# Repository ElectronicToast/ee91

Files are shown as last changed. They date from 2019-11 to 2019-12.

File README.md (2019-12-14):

# ee91
Analog autonomous vehicle project for EE 91 at Caltech

# Contributors
- Ray Sun - Caltech BS EE '20
- Evan Yeh - Caltech BS EE '20

# Licensing
With the exception of the Caltech logo, this project is licensed according to the terms of the MIT License. The Caltech logo is (c) California Institute of Technology and used to represent this project as part of Caltech's curriculum.

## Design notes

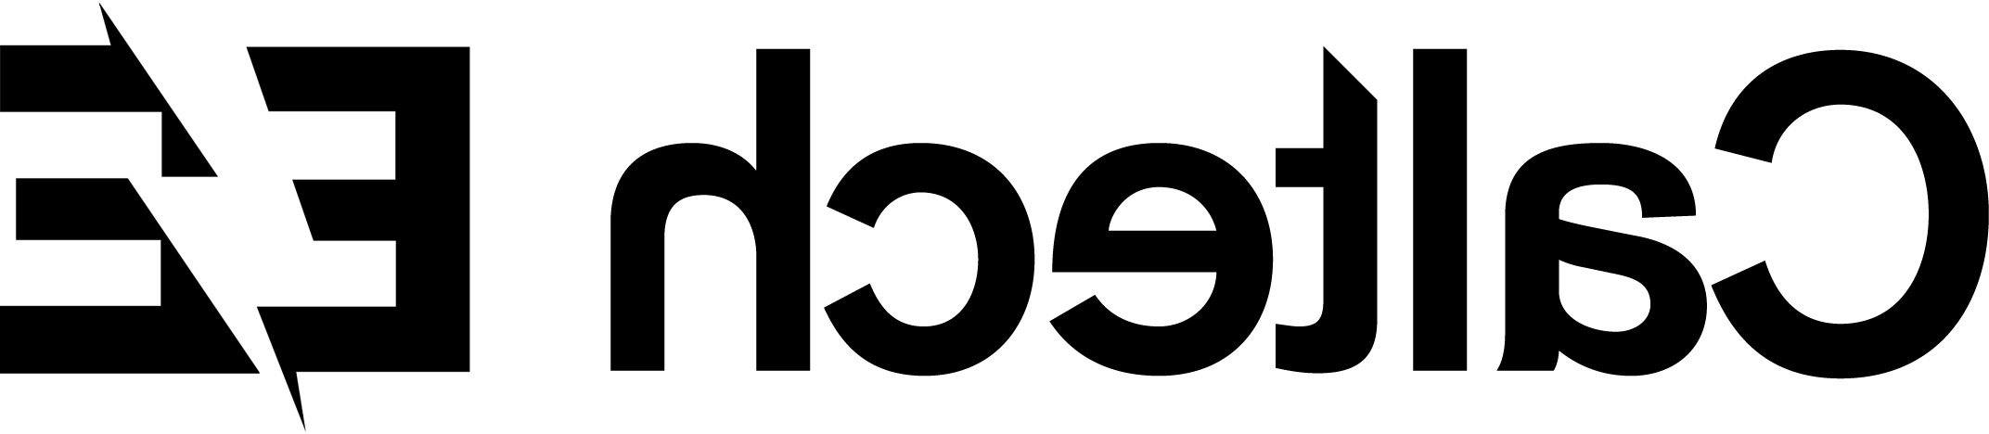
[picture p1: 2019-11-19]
Images/caltech_ee_bw_mirror.png

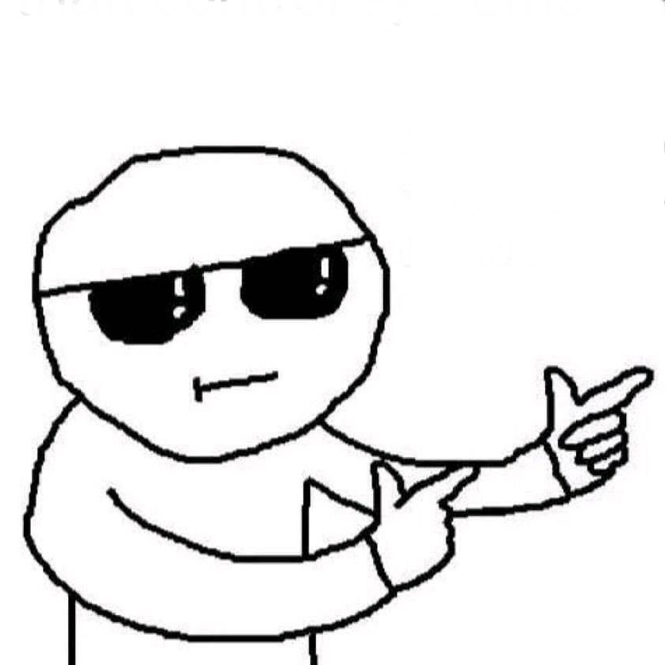
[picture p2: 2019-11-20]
Images/dude.jpg

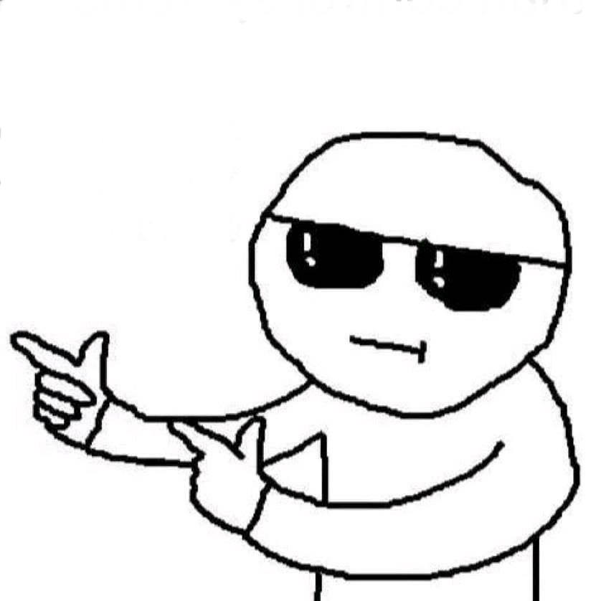
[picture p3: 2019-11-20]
Images/dude_reversed.jpg

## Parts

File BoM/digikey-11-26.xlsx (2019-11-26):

Index | Quantity | Part Number | Manufacturer Part Number | Description | Customer Reference | Available | Backorder | Unit Price | Extended Price USD
1 | 1 | 283-3029-ND | BK/GMA-200-R | FUSE GLASS 200MA 250VAC 5X20MM |  | 1 | 0 | 0.95 | 0.95
2 | 15 | 36-5005-ND | 5005 | PC TEST POINT COMPACT RED | TP_RED | 15 | 0 | 0.335 | 5.03
3 | 10 | 36-5006-ND | 5006 | PC TEST POINT COMPACT BLACK | TP_BLACK | 10 | 0 | 0.35 | 1.75
4 | 15 | 36-5007-ND | 5007 | PC TEST POINT COMPACT WHITE | TP_WHITE | 15 | 0 | 0.309 | 4.64
5 | 30 | 399-1177-1-ND | C0805C104Z5VACTU | CAP CER 0.1UF 50V Y5V 0805 | 0.1UF | 30 | 0 | 0.057 | 1.71
6 | 10 | 399-8039-1-ND | C0805C221M5RACTU | CAP CER 220PF 50V X7R 0805 | 220PF | 10 | 0 | 0.067 | 0.67
7 | 5 | 1276-2370-1-ND | CL10F334ZA8NNNC | CAP CER 0.33UF 25V Y5V 0603 | 0.33UF | 5 | 0 | 0.1 | 0.50
8 | 10 | RMCF0805FT3K90CT-ND | RMCF0805FT3K90 | RES 3.9K OHM 1% 1/8W 0805 | 3.9K | 10 | 0 | 0.027 | 0.27
9 | 10 | RMCF0805FT33K0CT-ND | RMCF0805FT33K0 | RES 33K OHM 1% 1/8W 0805 | 33K | 10 | 0 | 0.027 | 0.27
10 | 10 | RMCF0805FT39K0CT-ND | RMCF0805FT39K0 | RES 39K OHM 1% 1/8W 0805 | 39K | 10 | 0 | 0.027 | 0.27
11 | 10 | RMCF0805FT100KCT-ND | RMCF0805FT100K | RES 100K OHM 1% 1/8W 0805 | 100K | 10 | 0 | 0.027 | 0.27
12 | 5 | TC33X-102ECT-ND | TC33X-2-102E | TRIMMER 1K OHM 0.1W J LEAD TOP | 1K | 5 | 0 | 0.28 | 1.40
13 | 3 | TC33X-103ECT-ND | TC33X-2-103E | TRIMMER 10K OHM 0.1W J LEAD TOP | 10K | 3 | 0 | 0.28 | 0.84
14 | 5 | TC33X-104ECT-ND | TC33X-2-104E | TRIMMER 100K OHM 0.1W J LEAD TOP | 100K | 5 | 0 | 0.28 | 1.40
15 | 5 | 1N4148WTPMSCT-ND | 1N4148W-TP | DIODE GEN PURP 100V 150MA SOD123 |  | 5 | 0 | 0.13 | 0.65
16 | 3 | 296-1336-1-ND | TLC555CDR | IC OSC SGL TIMER 2.1MHZ 8-SOIC |  | 3 | 0 | 0.75 | 1.50
17 | 3 | 1727-6034-1-ND | 74HC1G04GV,125 | IC INVERTER 1CH 1-INP 5TSOP |  | 3 | 0 | 0.3 | 0.60
18 | 3 | 497-2345-1-ND | ULN2003D1013TR | IC PWR RELAY 7NPN 1:1 16SO |  | 3 | 0 | 0.52 | 1.04
19 | 10 | RMCF0805FT1K00CT-ND | RMCF0805FT1K00 | RES 1K OHM 1% 1/8W 0805 | 1k | 10 | 0 | 0.027 | 0.27
20 | 10 | RMCF0805FT10K0CT-ND | RMCF0805FT10K0 | RES 10K OHM 1% 1/8W 0805 | 10k | 10 | 0 | 0.027 | 0.27
21 | 15 | 399-17617-1-ND | C0805C103K1RAC7210 | CAP CER SMD 0805 .01UF 100V X7R | 0.01uF | 15 | 0 | 0.068 | 1.02
22 | 10 | 1276-6455-1-ND | CL21A106KOQNNNG | CAP CER 10UF 16V X5R 0805 | 10uF | 10 | 0 | 0.097 | 0.97
23 | 10 | RMCF0805FT4K70CT-ND | RMCF0805FT4K70 | RES 4.7K OHM 1% 1/8W 0805 | 4.7k | 10 | 0 | 0.027 | 0.27
24 | 3 | TC33X-2-504ECT-ND | TC33X-2-504E | TRIMMER 500K OHM 0.1W J LEAD TOP | 500k | 3 | 0 | 0.28 | 0.84
25 | 1 | 1568-DEV-15583-ND | DEV-15583 | TEENSY 4.0 |  | 1 | 0 | 22.5 | 22.50

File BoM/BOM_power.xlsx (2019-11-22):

RefDes | Value | Name | Manufacturer | Quantity | Buy
VCC, -VCC |  | TESTPOINT RED |  | 2 | https://www.digikey.com/products/en?mpart=5005&v=36
GND |  | TESTPOINT BLACK |  | 1 | https://www.digikey.com/product-detail/en/keystone-electronics/5006/36-5006-ND/255330
J1, J2, J3, J4 |  | JST_XH_3 |  | 4 | https://www.digikey.com/product-detail/en/jst-sales-america-inc/B3B-XH-A-LF-SN/455-2248-ND/1651046
J5, J6 |  | JST_XH_2 |  | 2 | https://www.digikey.com/product-detail/en/jst-sales-america-inc/B2B-XH-A-LF-SN/455-2247-ND/1651045

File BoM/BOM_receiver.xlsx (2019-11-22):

RefDes | Value | Name | Manufacturer | Quantity | Buy
VCC, -VCC |  | TESTPOINT RED |  | 4 | https://www.digikey.com/products/en?mpart=5005&v=36
GND |  | TESTPOINT BLACK |  | 2 | https://www.digikey.com/product-detail/en/keystone-electronics/5006/36-5006-ND/255330
BP, GAIN, US_IN |  | TESTPOINT WHITE |  | 6 | https://www.digikey.com/product-detail/en/keystone-electronics/5007/36-5007-ND/255331
C7, C8 | 0.01uF | CAP_0805 |  | 4
C3, C4, C5, C6, C9 | 0.1uF | CAP_0805 |  | 10
C1, C2 | 220pF | CAP_0805 |  | 4
C10, C11 | 10uF | CAP_0805 |  | 4
R3 | 3.9k | RES_0805 |  | 2
R1 | 4.7k | RES_0805 |  | 2
R5 | 10k | RES_0805 |  | 2
R4 | 100k | RES_0805 |  | 2
D1 |  | 1N4148 |  | 2 | https://www.digikey.com/product-detail/en/on-semiconductor/1N4148WS/1N4148WSFSCT-ND/1873821
J1, J2 |  | JST_XH_2 | JST | 4 | https://www.digikey.com/product-detail/en/jst-sales-america-inc/B2B-XH-A-LF-SN/455-2247-ND/1651045
J3 |  | JST_XH_3 | JST | 2 | https://www.digikey.com/product-detail/en/jst-sales-america-inc/B3B-XH-A-LF-SN/455-2248-ND/1651046
R2 | 500k | TC33X-2_500k | Bourns | 2 | https://www.digikey.com/product-detail/en/bourns-inc/TC33X-2-504E/TC33X-2-504ETR-ND/2566902
U1 |  | AD826AR | Analog Devices | 2 | https://www.digikey.com/product-detail/en/analog-devices-inc/AD826ARZ/AD826ARZ-ND/620949

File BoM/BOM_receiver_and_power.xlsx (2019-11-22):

Value | Name | Manufacturer | Quantity | Buy
 | TESTPOINT RED |  | 6 | https://www.digikey.com/products/en?mpart=5005&v=36
 | TESTPOINT BLACK |  | 3 | https://www.digikey.com/product-detail/en/keystone-electronics/5006/36-5006-ND/255330
 | TESTPOINT WHITE |  | 6 | https://www.digikey.com/product-detail/en/keystone-electronics/5007/36-5007-ND/255331
0.01uF | CAP_0805 |  | 4
0.1uF | CAP_0805 |  | 10
220pF | CAP_0805 |  | 4
10uF | CAP_0805 |  | 4
3.9k | RES_0805 |  | 2
4.7k | RES_0805 |  | 2
10k | RES_0805 |  | 2
100k | RES_0805 |  | 2
500k | TC33X-2_500k | Bourns | 2 | https://www.digikey.com/product-detail/en/bourns-inc/TC33X-2-504E/TC33X-2-504ETR-ND/2566902
 | 1N4148 |  | 2 | https://www.digikey.com/product-detail/en/on-semiconductor/1N4148WS/1N4148WSFSCT-ND/1873821
 | JST_XH_2 | JST | 6 | https://www.digikey.com/product-detail/en/jst-sales-america-inc/B2B-XH-A-LF-SN/455-2247-ND/1651045
 | JST_XH_3 | JST | 6 | https://www.digikey.com/product-detail/en/jst-sales-america-inc/B3B-XH-A-LF-SN/455-2248-ND/1651046
 | AD826AR | Analog Devices | 2 | https://www.digikey.com/product-detail/en/analog-devices-inc/AD826ARZ/AD826ARZ-ND/620949

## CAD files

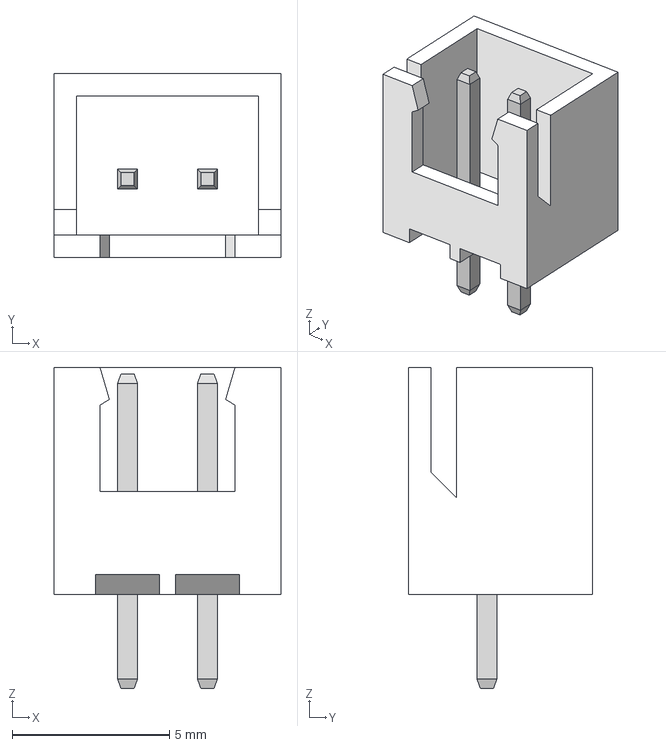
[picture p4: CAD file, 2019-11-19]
3D Models/JST - XH - Thru (V) - 2Pin - 2.54mm.stp
7.21 x 5.84 x 10.2 mm

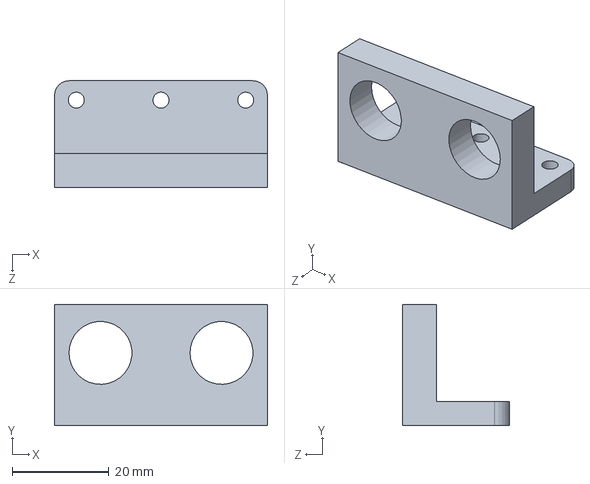
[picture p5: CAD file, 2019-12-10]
3DPrints/transducermount/transducermount.SLDPRT
44.0 x 25.0 x 22.0 mm

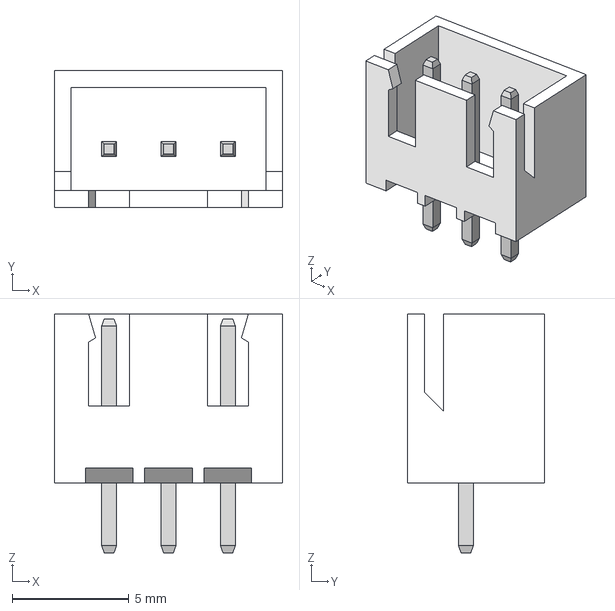
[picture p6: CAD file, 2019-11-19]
3D Models/JST - XH - Thru (V) - 3Pin - 2.54mm.stp
9.75 x 5.84 x 10.2 mm

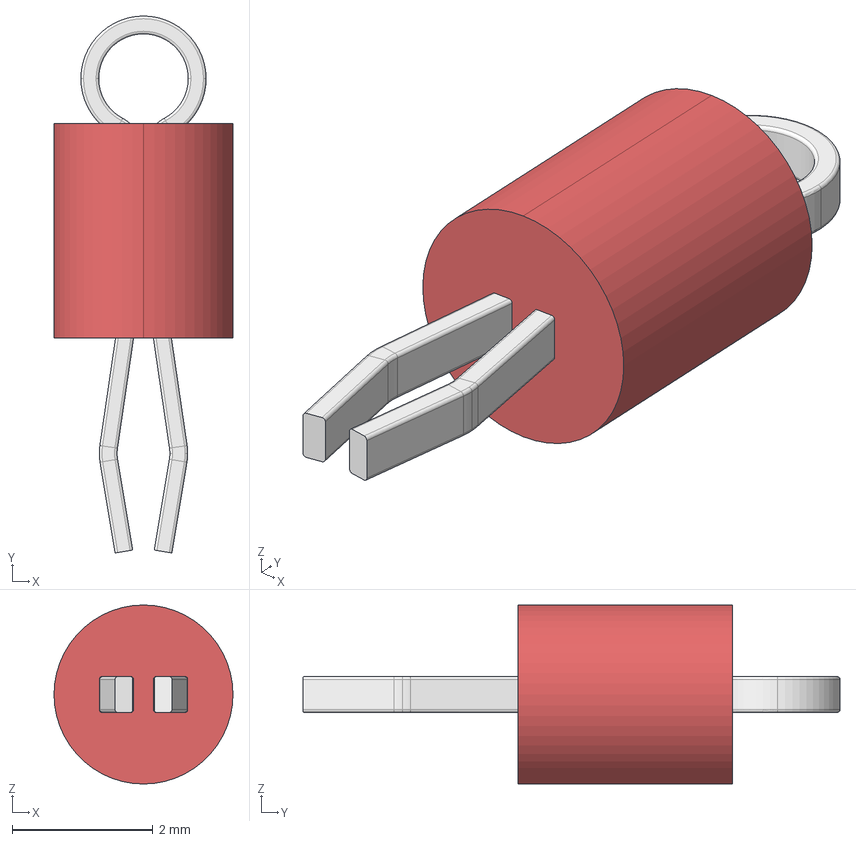
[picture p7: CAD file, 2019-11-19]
3D Models/5005 red.step
2.54 x 7.62 x 2.54 mm

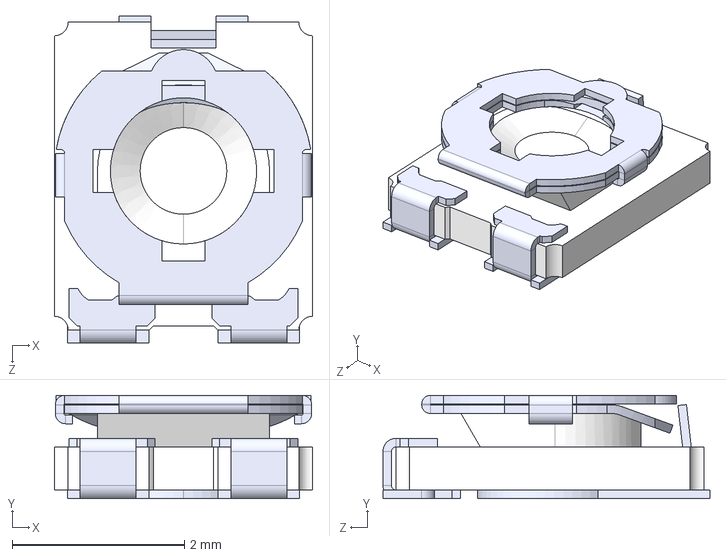
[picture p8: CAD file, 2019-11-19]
3D Models/TC33X-2.STEP
3.00 x 1.20 x 3.80 mm

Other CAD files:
3DPrints/transducermount/transducermount.STL

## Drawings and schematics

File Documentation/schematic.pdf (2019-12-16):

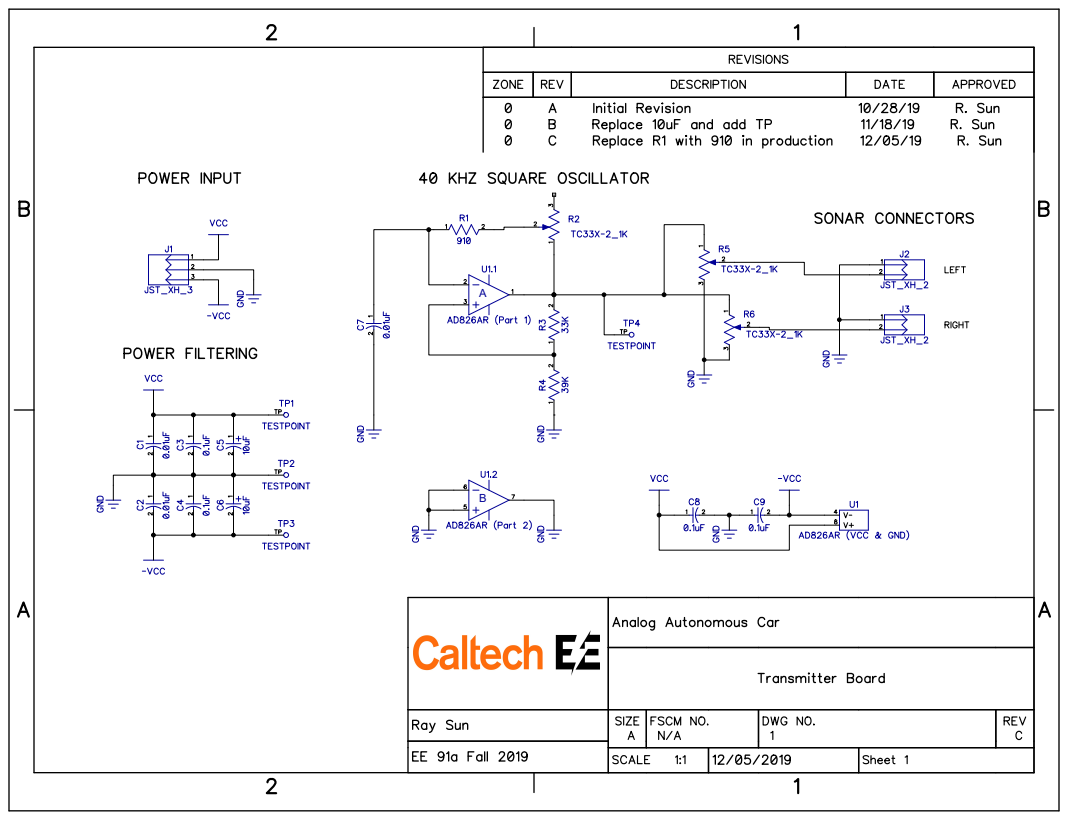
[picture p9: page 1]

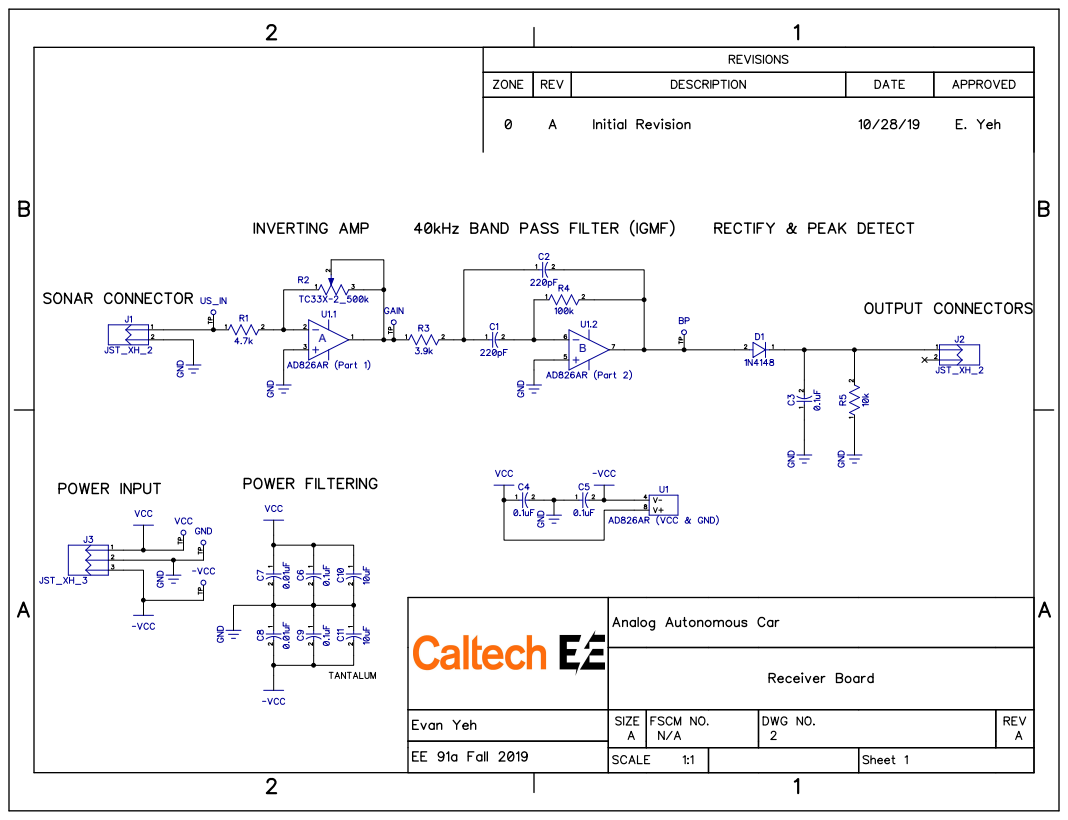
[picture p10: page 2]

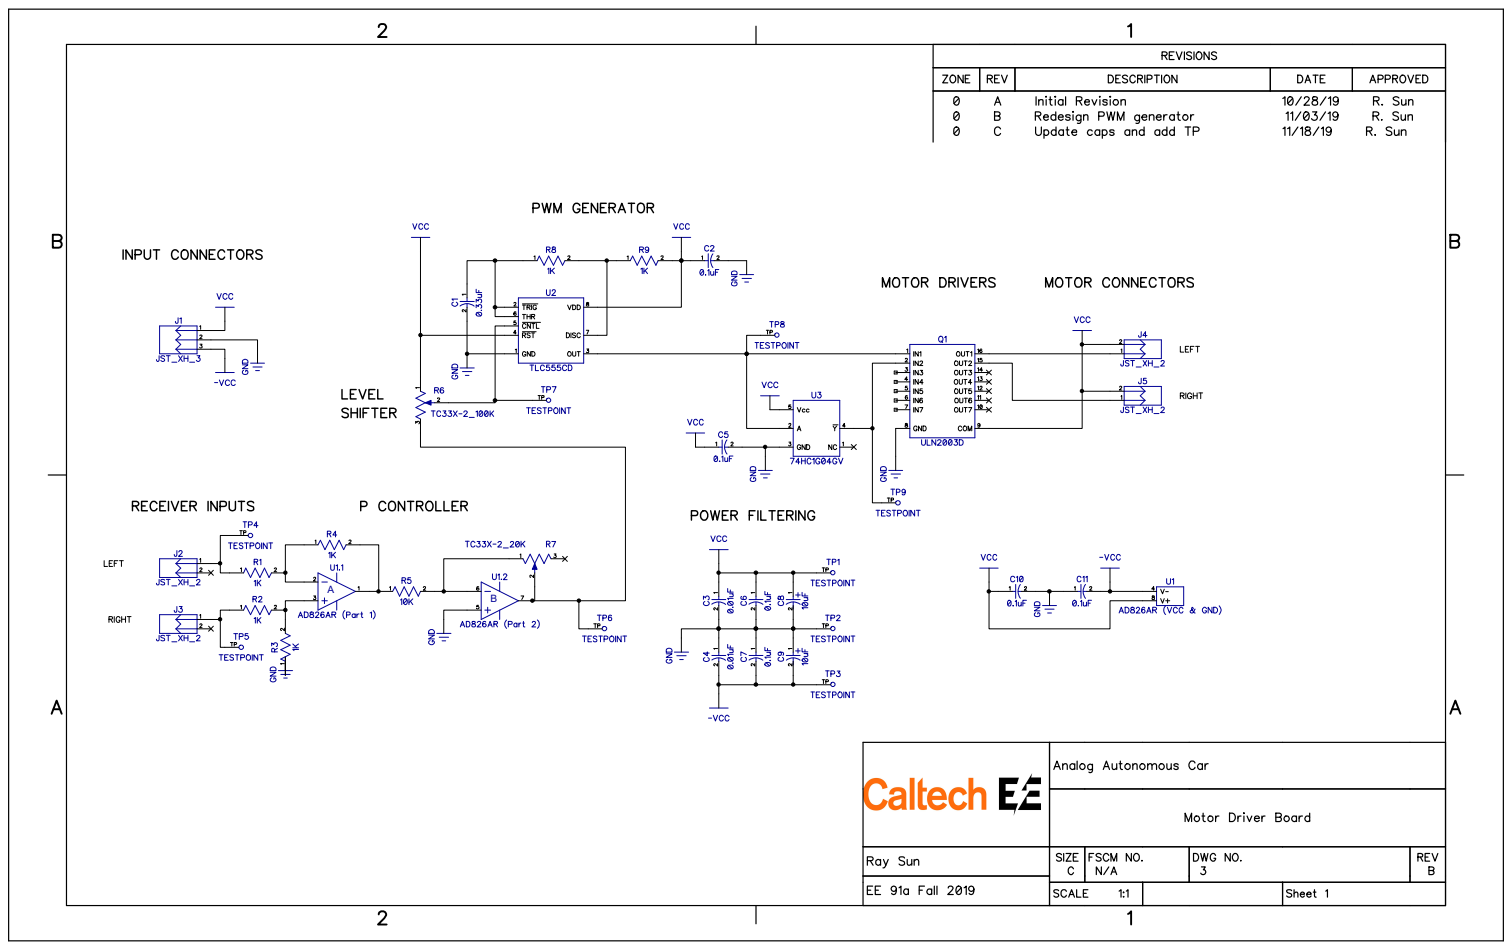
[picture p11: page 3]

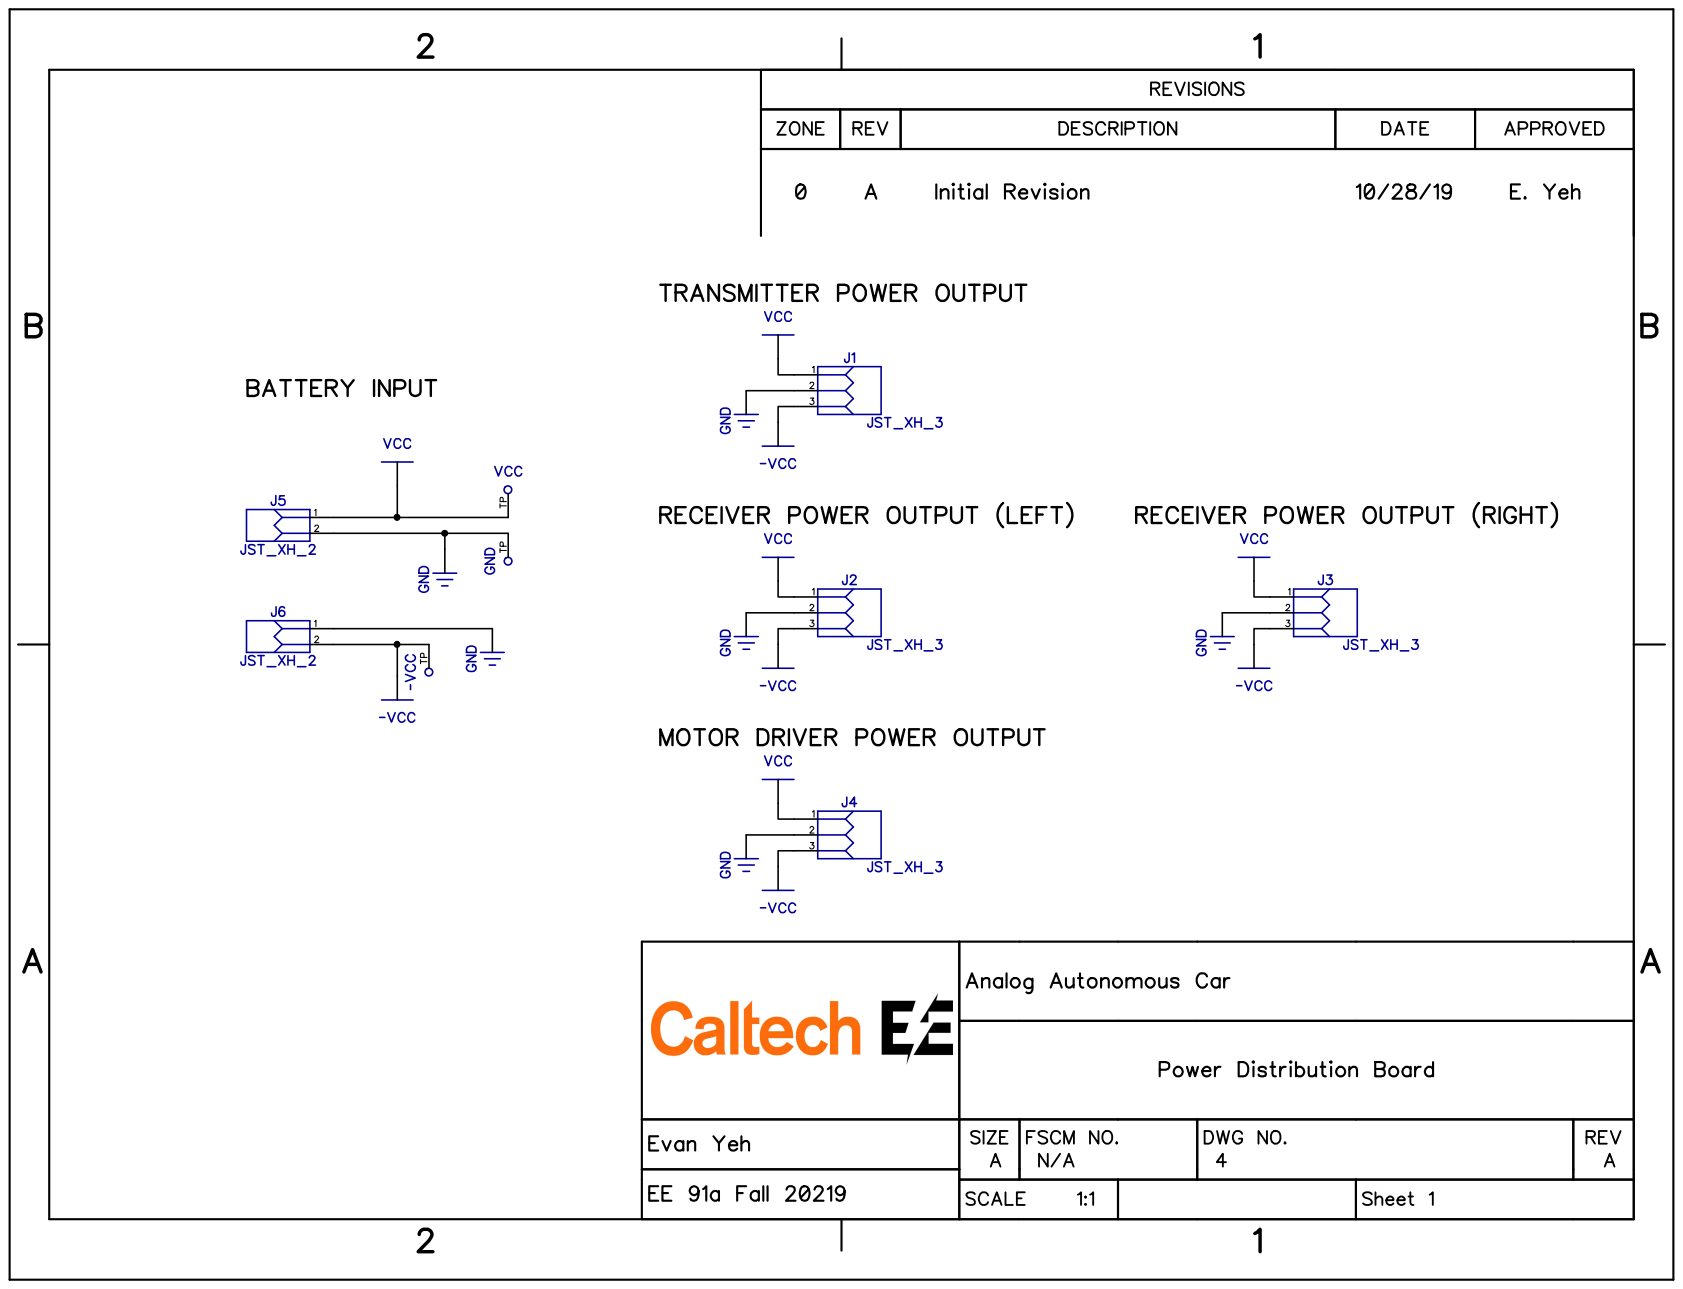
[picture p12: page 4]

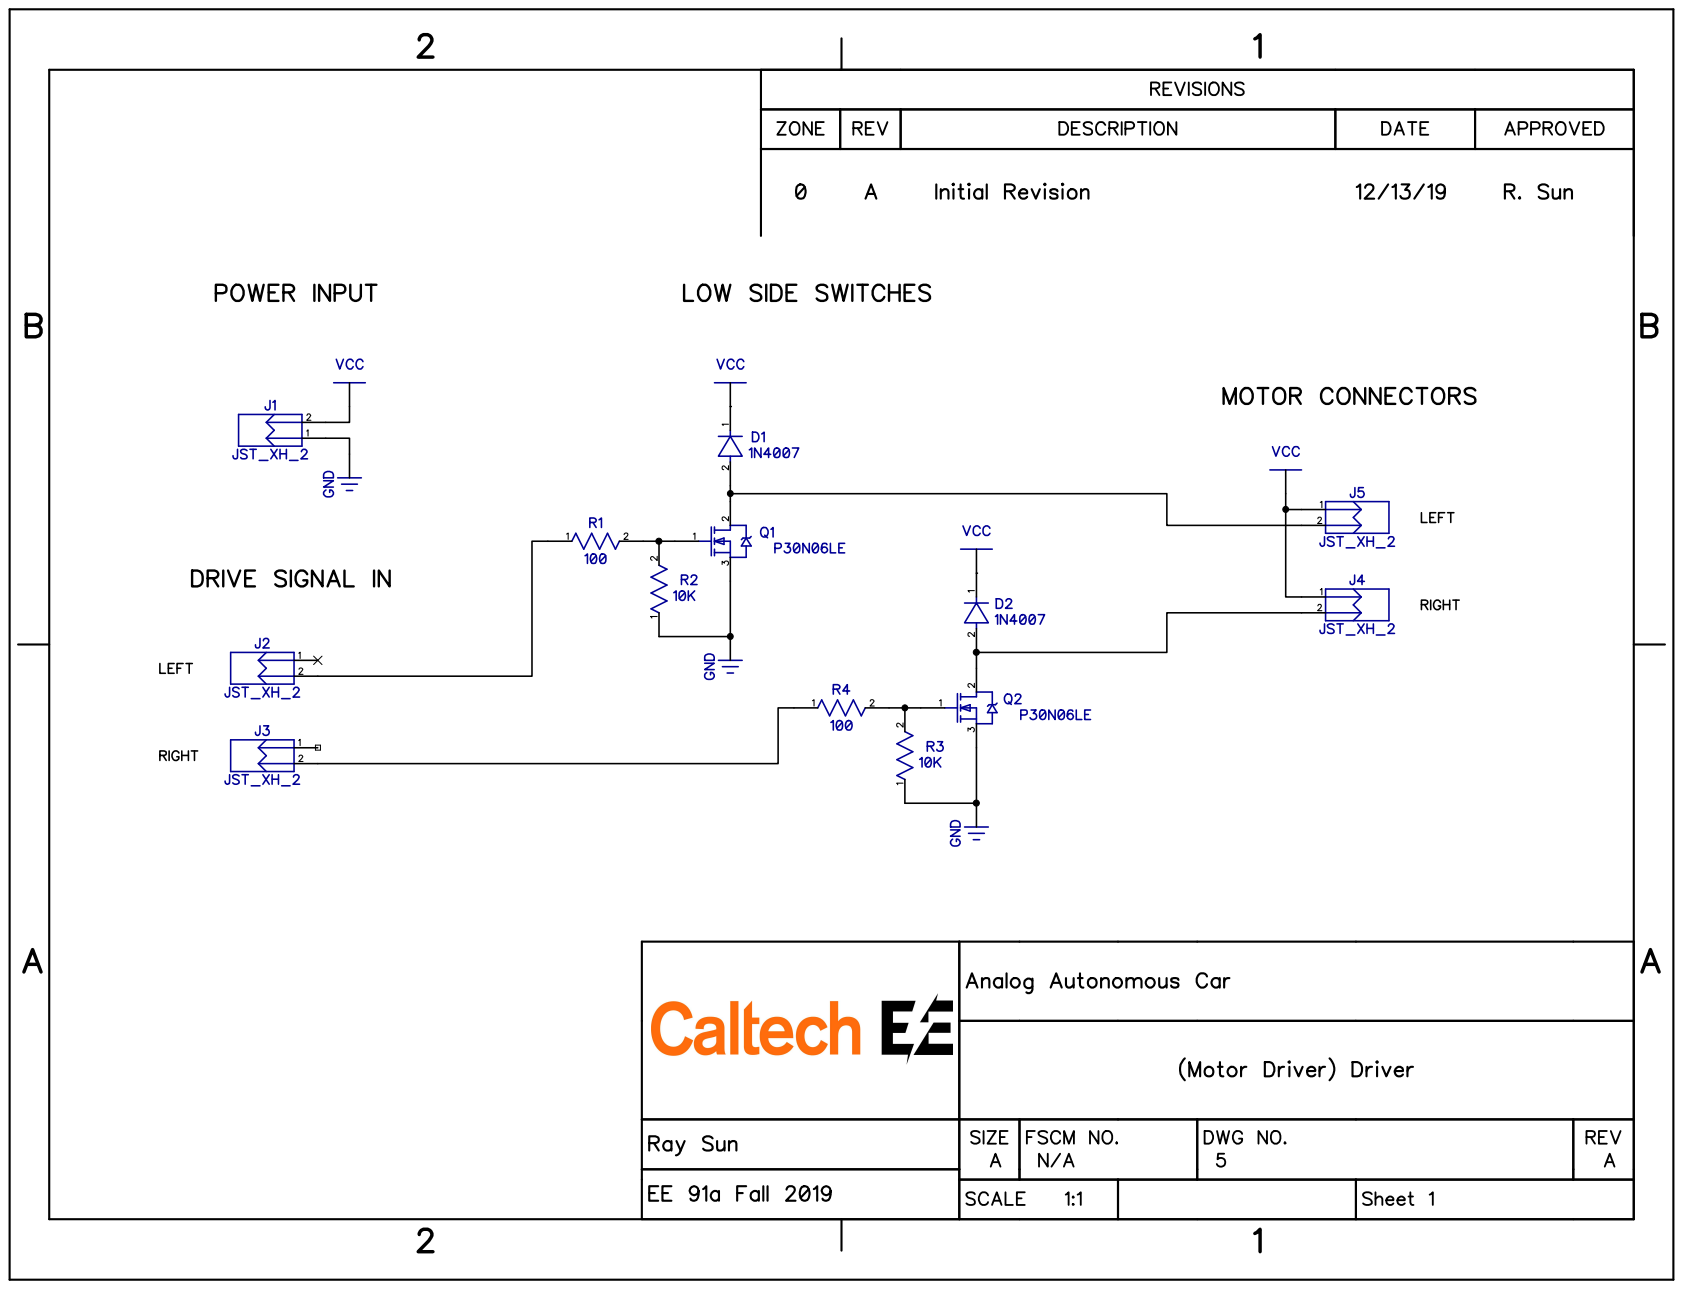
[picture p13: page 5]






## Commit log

2019-10-28 Start schematic for receiver board
2019-10-28 Add transmitter board schematic
2019-10-28 Add motor driver board
2019-10-28 Fix output connecter pin orientation
2019-10-28 Add power distribution board
2019-11-04 Add initial simulation files for transmitter and motor driver
2019-11-04 Simplify motor driver oscillator design
2019-11-04 Add simplified motor driver PWM simulation
2019-11-04 Simplify motor PWM generator circuit
2019-11-04 Add simulation for receiver board
2019-11-05 Add simulation for subtracter circuit
2019-11-05 Add noisy simulation files for motor driver and transmitter
2019-11-10 Add power noise simulation
2019-11-10 Add DipTrace symbol/component libraries with Glen's EE lib + JST XH 2,3 connectors
2019-11-11 Lay out motor driver
2019-11-11 Place transmitter board
2019-11-12 Add power pcb placement
2019-11-12 Add receiver pcb placement
2019-11-12 Recover simulation with power noise
2019-11-18 Route most of motorboard
2019-11-18 Add testpoints for power
2019-11-18 Add power testpoints
2019-11-18 Add footprint for testpoints
2019-11-18 Update caps and add TP (currently small ones)
2019-11-19 Add 3D models for testpoint, jst 2/3 pins, pot
    [5005 red.step, JST - XH - Thru (V) - 2Pin - 2.54mm.stp, JST - XH - Thru (V) - 3Pin - 2.54mm.stp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]
2019-11-20 Prettify motor driver
2019-11-20 Add +-VCC power planes
2019-11-20 Route traces away from test points and round board edge
2019-11-22 Disconnect output ground
2019-11-22 Add BOM for receiver and power dist boards
    [BOM_power.xlsx, BOM_receiver.xlsx, BOM_receiver_and_power.xlsx]
2019-11-22 More sensible power routing and increase hole size to 0.125 in
2019-11-22 Standardize hole size to 0.125 in, 0.15 in keepout
2019-11-22 Move TP away from mounting holes
2019-11-22 Rearrange TP and holes for screw head clearance
2019-11-23 Generate Gerbers
    [BoardOutline.gbr, Bottom.gbr, BottomMask.gbr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]
2019-11-23 Regenerate to fix tented vias
    [Bottom.gbr, BottomMask.gbr, Top.gbr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]
2019-11-23 Change logo font
    [Bottom.gbr, BottomMask.gbr, BottomSilk.gbr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]
2019-11-23 Add ICs
    [BOM_TOTAL.xlsx]
2019-11-26 Add Digikey part numbers
    [BOM_TOTAL.xlsx]
2019-11-26 Order parts
    [BOM_TOTAL.xlsx, digikey-11-26.xlsx]
2019-12-06 Add schematic for transmitter as soldered
2019-12-07 Make title blocks consistent and generate schematic prints
2019-12-10 Add transducer mount 3D print
    [transducermount.SLDPRT, transducermount.STL]
2019-12-14 Add motor driver driver perfboard schematic
2019-12-16 Add combined schematic
